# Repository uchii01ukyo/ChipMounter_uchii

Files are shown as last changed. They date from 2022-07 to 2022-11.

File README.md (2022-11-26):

# ChipMounter
電子部品を基板上の指定した位置に配置してくれる機構  
  
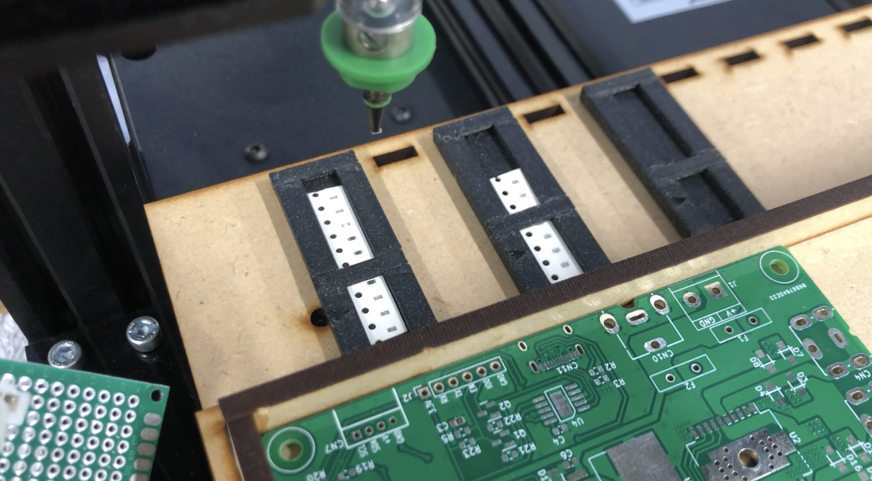
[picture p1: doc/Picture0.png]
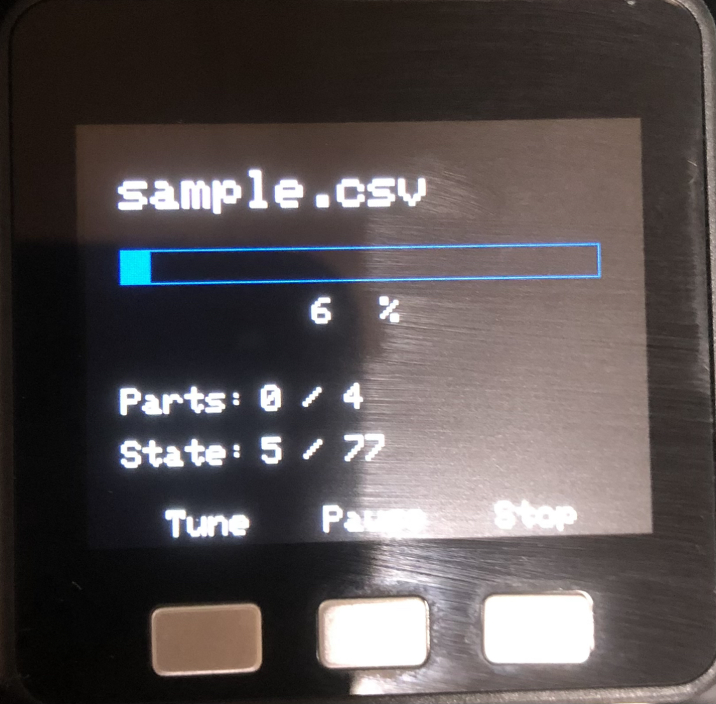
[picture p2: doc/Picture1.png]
  
  
3つのステップモーターでXYZ軸移動、別モーターでZ軸回転、吸引ポンプと吐出ポンプで部品のピッキングをしている．  
  
詳細：[ChipMounter_System.pdf](https://github.com/uchii01ukyo/ChipMounter_uchii/blob/master/doc/ChipMounter%20System.pdf)  
デモ：[demo0.mp4](https://github.com/uchii01ukyo/ChipMounter_uchii/blob/master/doc/demo0.mp4)    

以下のコードを参考にさせていただきました．  
参考：https://github.com/akita11/ChipMounter  

## 使い方
### CSVファイルの準備
実装部品の位置や角度はCSV形式のファイルから読みとる．  
1. KiCADから実装基板の部品情報（POSファイル）をCSVで出力する．  
2. CSVファイルの一番右に新しい行を挿入し、部品に対応するTrayIDを入力する．  
3. 「src/csv_gcode.py」の以下の部分をPOSファイルのパスに変更する．  
  
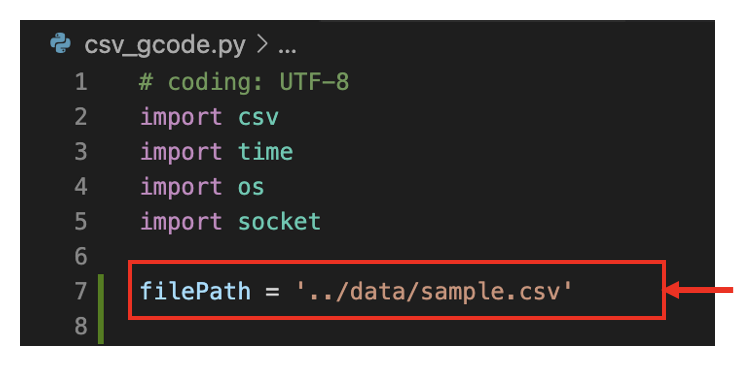
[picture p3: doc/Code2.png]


### 起動
1. M5Stackと使用するPCをUSBで接続する  
2. M5Stackを再起動する（画面に「Chip Mounter」が表示されている状態にする）  
3. start.commandを実行(クリックするだけでOK)  

### 起動後
起動後、PC上では２つのコマンドプロンプトが開かれ、GCODEの生成->送信が実行される．  
M5Stackではコマンドを受信し、それに合わせてアクチュエータ制御、画面表示等を実行する．  

## その他
### GRBLモジュールについて
非常にクセがあって苦労したので、ドキュメントを残すことにした．  
[M5Stack_GRBL_Module.pdf](https://github.com/uchii01ukyo/ChipMounter_uchii/blob/master/doc/M5Stack%20GRBL%20Module.pdf)  
  
### 注意
BOMおよびその他のデータは、著者によってのみテストされています。情報の不足や誤り、バグがある可能性があります。  
  
### テスト環境
以下の環境で実証済みです．
+ MacOS Big Sur (11.6.8)
+ Python 2.7.18
+ ArduinoIDE 1.8.13

## Author
Uchii Ukyo　(https://github.com/uchii01ukyo)

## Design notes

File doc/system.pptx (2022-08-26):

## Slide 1

PC

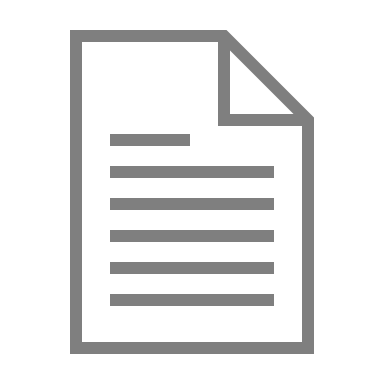
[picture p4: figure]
ドキュメント 枠線

M5Stack-CORE

M5_Serial.ino
GRBLControl.cpp
GRBLControl.h

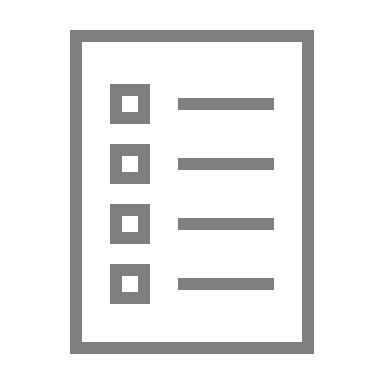
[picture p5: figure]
リスト 枠線

data.csv

read

UDP

Serial

csv_gcode.py

udp_serial.py

I2C
(0x70)

I2C
(0x71)

Digital
Write

GRBL-1

GRBL-2

Solenoid

Pump-1

X

Y

Z

R

Pump-2

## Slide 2

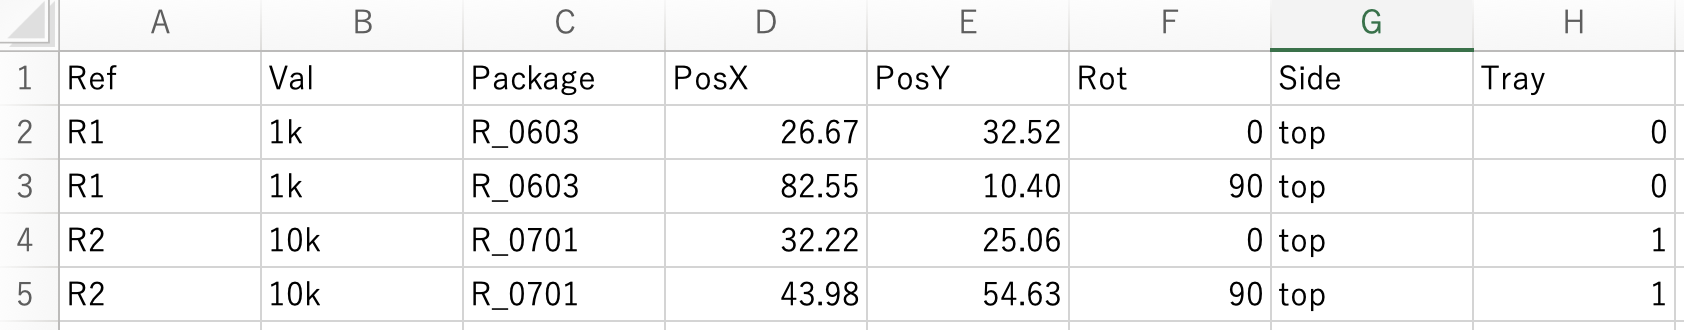
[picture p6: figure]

新しい行を挿入
→ TrayIDを入力

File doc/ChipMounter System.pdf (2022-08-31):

# ChipMounter System

全体のシステム概要図

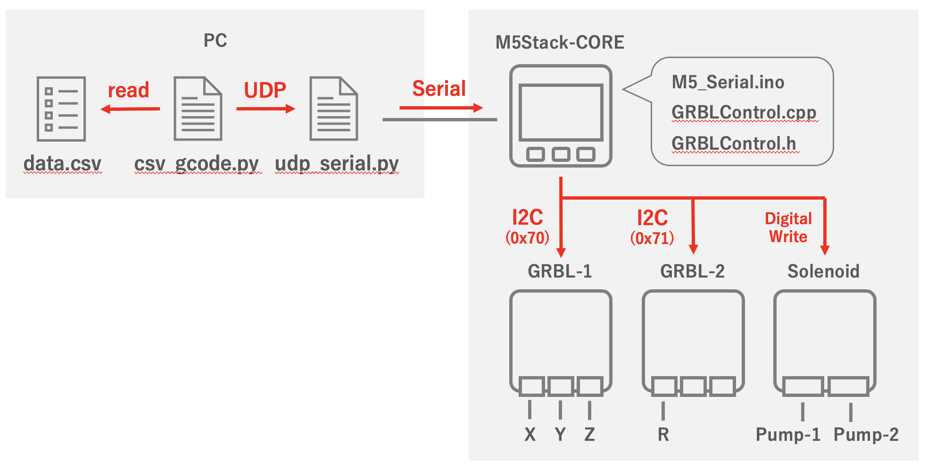
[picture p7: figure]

概要
- 制御するものは5つ
（X-StepMotor, Y-StepMotor, Z-StepMotor, 回転軸Motor, 吸ポンプ, 吐ポンプ）
- CSVで指定した部品位置に部品を配置する
- 作成したGcodeを、 udp_serial.py → M5_Serial.ino → GRBLの順に流すことでステップ モータ等を制御している

各コードの役割
- csv_gcode.py
= POSファイル（CSV形式）から、部品位置を抽出して、Gcodeを作成
= 作成したGcodeをUDP通信で送信
- udp_serial.py
= M5Stackとのシリアルを常時開通させ、Gcodeの送信、GRBLステータスの受信
- M5_Serial.ino
= Gcodeの受信、適切なモジュール（GRBL-1, GRBL-2, Soleoid）に送信
= 画面表示などのUI管理

## データ処理の流れ

## csv_gcodeの処理

処理の流れ
- CSVファイルから、POSデータ（部品の配置位置など）を読み取る
- POSデータからcommandを作成する
- 作成したcommandをudp_serial.py（UDP通信）、M5Stack-CORE（Serial通信）で受け渡 す
- 処理成功の合図（’ok’）を待ってから、次のcommandを送信
- commandを全部送信し切ったら、次の部品に関するPOSデータを取得しにいく

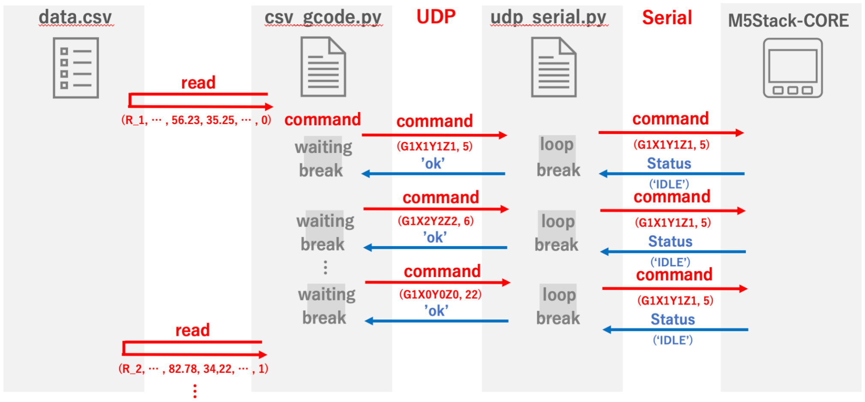
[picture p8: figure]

## udp_serial.pyの処理

処理の流れ
- csv_gcode.pyからcommandを受信する
- 受信したcommandをそのままM5Stack-COREに受け渡す
- スタータス確認コマンド（’@’）を送信して、現在のステータスを返してもらう
- ステータス’IDLE’を確認しだい、処理成功の合図として’ok’を送信する

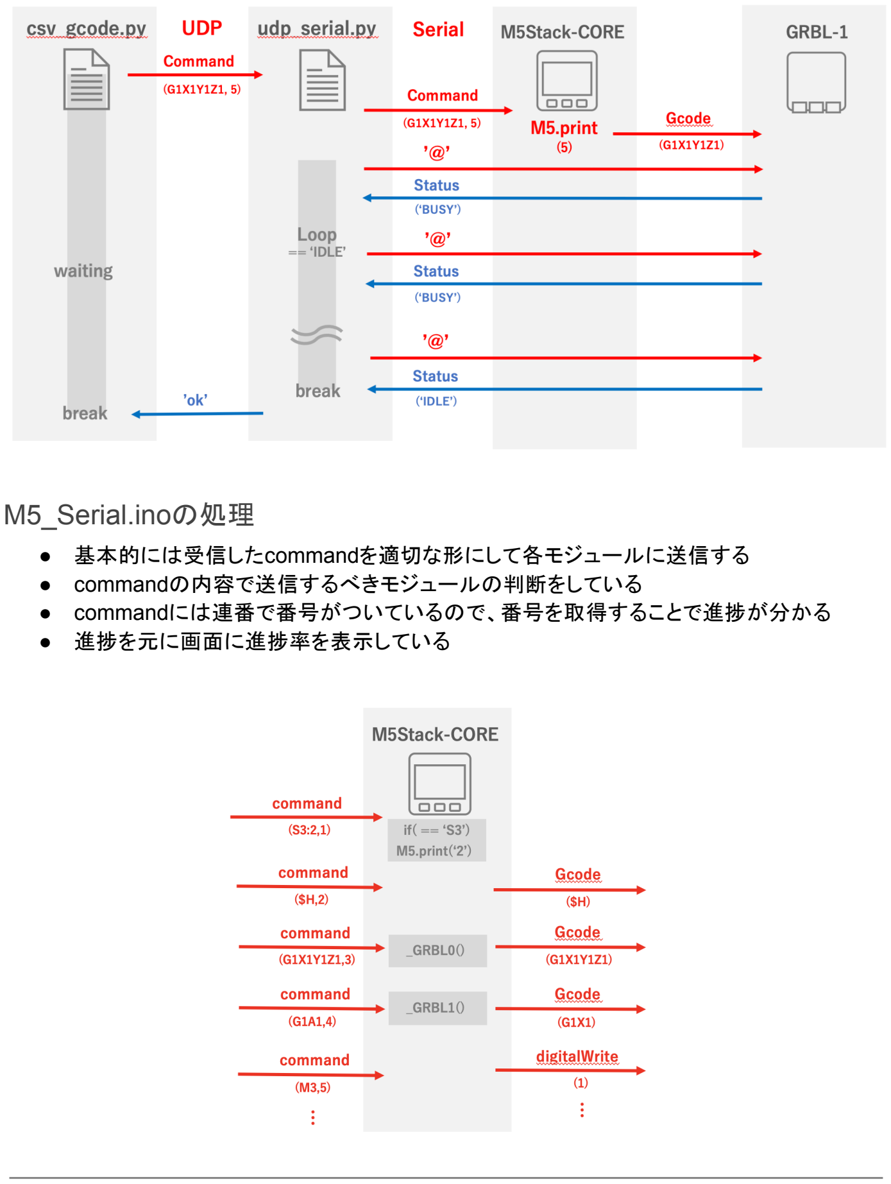
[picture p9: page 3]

## M5_Serial.inoの処理

- 基本的には受信したcommandを適切な形にして各モジュールに送信する
- commandの内容で送信するべきモジュールの判断をしている
- commandには連番で番号がついているので、番号を取得することで進捗が分かる
- 進捗を元に画面に進捗率を表示している

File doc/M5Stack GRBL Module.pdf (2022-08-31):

# M5Stack GRBL 13.2

2022.08.27 内井

公式ドキュメント：https://docs.m5stack.com/en/module/grbl13.2サンプルコード：https://github.com/m5stack/MODULE_GRBL13.2/tree/master

概要
- M5Stackで使用できるGRBLモジュール
- Motor Driver: DRV8825PWPR
- Controller Chip: ATmega328P-AU
- 1台で最大3つのステップモータを制御できる
- I2Cアドレスを変更すれば２台スタック可能
- 外部リミットスイッチを接続できる
- コマンドはGRBL0.8系で通用する

GRBL0.8系：https://github.com/grbl/grbl/wiki/Configuring-Grbl-v0.8

## はじめに

チップマウンター（基板部品を基板上に配置してくれる機構）を作ることに挑戦し、その時にGRBL を用いてステップモーターを制御するということをやった． そこでほぼ初めてGRBLを使ってモノづくりをしてみたが、以下の壁にぶつかった．

- GRBLについての情報がネットにあまり載っていない
（M5Stack GRBL 13.2に関する情報なんてほとんどない）
- いろんなバージョンが混ざってよく分からない
（Arduinoとか、CNCオープンソースとか．GRBLにも0.8系と0.9系と1.1系がある）
- そもそもGRBLについての基礎知識すらなくてよく分からない

とにかく情報がなく、公式ドキュメントを読めるだけの知識もなく、自力でしらみつぶしで検証する ことが多かった．
結局分からなかったものもあるが、多くは正解に辿り着いたと思う． 結果的に、公式ドキュメントが間違っていたり、公式のサンプルコードが間違っていたりと、いろい ろと穴だらけだった．またそもそも初心者つぶしのトラップがいくつも潜んでいることが分かった．

今後の自分のために、そして誰かのためにもドキュメントを残しておく．

## GCODE

初心者のために．そもそもGcodeとは何か、ステップモーターをどうやって動かすのか．

### ステップモータを動かす

動かし方１：
M5StackとArduinoIDEをUSBで接続する（シリアル通信ができる状態にする） M5StackにM5_serial.inoを書き込む
シリアルモニタの入力窓から、コマンドを入力する．
例えば、G91G0X1Y1Z1、と入力すれば現在位置から相対座標で（1,1,1）に動いてくれる．

動かし方２：
M5_Serial.inoのLoop関数内に、以下のコードを入れる． 「if(M5.BtnA.wasPressed()){ _GRBL0.Gcode(“G91G0X1Y1Z1”);」 M5StackとArduinoIDEをUSBで接続する（シリアル通信ができる状態にする） M5StackにM5_serial.inoを書き込む．
M5StackのAボタンを押す．

### ステップモータが動かない

いくつかよくあるミスを書いておく．

・供給されている電圧が低い / 電源が供給されていない パソコン給電ではなく、ACアダプタ等の外部電源が必要（適切な供給電圧で）

・配線がうまくされていない
ステップモーターには大きくユニポーラ式とバイポーラ式がある． またコードが途中で（親切心から）クロスしているものもある． ステップモータの種類によって配線が違うので、ドキュメントを見ながら配線する． 特に４線のうち真ん中２本がどう繋がっているかが問題になりやすい．違った場合は真ん中２本 だけをハンダで繋ぎかえるなどの対応をする

・GRBLライブラリが入っていない
ファームウェアはGRBLモジュール側に事前に書き込まれているため、不要． しかしM5Stack本体にはGRBLライブラリ（例えば、GrblControl.hとGrblControl.cppなど）を書き 込む必要がある．制御コードにインポートさせておくと良い．

・内部変数が適切でない
後述の内部変数の設定が適切でない場合がある．
（パルスが細かすぎてモータが動かない、トルクが足りなくて動かない等） 内部変数を見直してみると良い．

・ロックがかかっている
$17を1に設定していると、初めは必ずロック状態になる．ロック状態ではどの小アンドも機能し ない．$Xか$Hで解除してからコマンドを入力するか、初めから$17を0にしておく シリアル通信でコマンド”@”を送信すると、現在のステータスを返してくれる．「ALART」と返って きた場合は、ロック状態である可能性が高い．（問題なければ「IDLE」と返ってくる）

## 内部変数 / Internal variable

GRBLではモーターの速度やパルスの周期などのパラメータを事前に書きこんでおく． 各変数は書き込んだ時点で、自動でEEPROMに保存される． ただ何かのエラーの影響で、変数が知らない間に変更されることがあるので、挙動が急におかし くなった時は、変数が正常に設定されているか確認すると良い．

### 内部変数の設定方法

ArduinoIDEとGRBLモジュールをUSBでつなぐ（シリアル通信できるようにする） シリアルモニタを開いて、入力窓から直接入力するのが、一番簡単． 以下のようにArduino上に含めておけば、そこからモジュールに書き込むこともできる． （注意：一度に５つ以上の変数は設定できない）

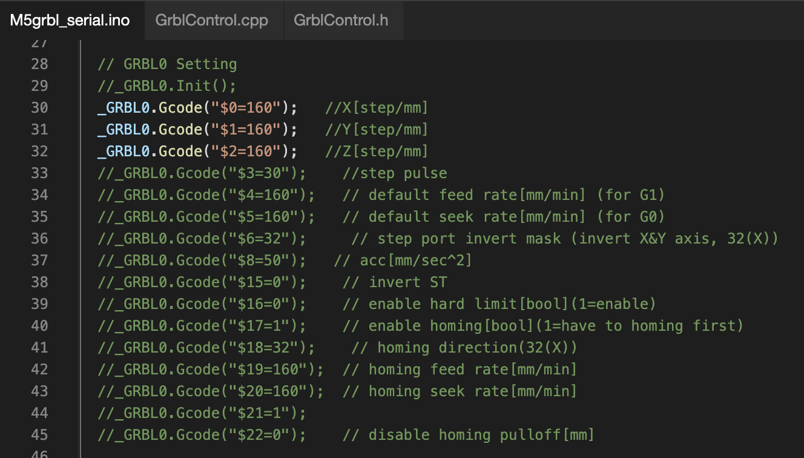
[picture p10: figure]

### 内部変数の設定

公式ドキュメントに記載されているものは誤りなので、気をつけること． Arduino式と設定内容が違うので注意すること（ネットのものはだいたいArduino式） 以下、実践の下、正しいと思われるものを載せる．

$0 = x [step/mm] 脱調（振動、騒音）している場合はここを変更すると良い
$1 = y [step/mm]
$2 = z [step/mm]
$3 = step pluse
$4 = feed rate [mm/min] (for G1)
$5 = seek rate [mm/min] (for G0)
$6 = step port invert mask 設定の仕方は後述 $8 = acc [mm/sec^2]
$10 = settings.mm_per_arc_segment
$11 = settings.n_arc_correction
$12 = settings.decimal_places

$13 = REPORT INCHES
$14 = BITFRAG_AUTO_START (=1)
$15 = invert ST (0=default, 1=モータの動作/停止が反対)
$16 = enable hard limit (0=disable, 1=enable)
$17 = enable homing (0=disable, 1=enable) 1だとhoming($H)されるまでlockされる $18 = settings.homing_dir_mask 設定の仕方は後述
$19 = settings.homing_feed_rate
$20 = settings.homing_seek_rate
$21 = settings.homing_debounce_delay homingを確かめる時間スパン[msec] $22 = settings.homing_pulloff homingした後に少し戻る

各変数について詳しい説明
（少し数字と内容が違うかもしれないが、参考程度に．） https://github.com/grbl/grbl/wiki/Configuring-Grbl-v0.8

## $6, $18の設定方法

$6 = default時の軸の正方向を指定する
$18= homing時の軸の正方向を指定する

各軸にビットが指定されている (X=5, Y=6, Z=7)． 1をこれだけビットシフトしたものの論理和として指定する．

分かりやすく言うと、
軸それぞれに以下の数字が与えられている
X = 00100000 (2進数表記) = 32 (10進数表記)
Y = 01000000 (2進数表記) = 64 (10進数表記)
Z = 10000000 (2進数表記) = 128 (10進数表記)

変更したい軸の数字を全て足したものを10進数で指定する． （例）
X軸だけを変更したい (32(X)なので) $6=32 X軸とY軸を変更したい (32(X)+64(Y)=96) $6=96 3軸ともに変更したい (32(X)+64(Y)+128(Z)) $6=224

### 内部変数を設定する時の注意点

モジュールのバッファサイズが小さいので注意

一般的なGRBLでは、コマンド “$$” を入力すると、内部変数の一覧を書き出してくれるようになっ ている（自分が過去に何を設定したかが分かるようになっている）．

M5Stack GRBL13.2でも同様のコマンドがあるが、バッファサイズの都合で10byteしか出力でき ない．なので、ほとんど見れない（$0〜$4くらいまでは見れる）．設定した数字はどこかにメモって おくか、しっかり設定できているか不安ならばその都度書き込むしかない．

また内部変数の設定は1つずつ行うのが最善．バッファサイズが10byteしかないので、一度に大 量の変数（5つ以上）を書き込むと全部書き込めない．オーバーした分は書きこまれないので注意 ．

## GRBLコマンド

GRBLは特定のコマンドを用いて操作する．
よく使うものをいくつか載せておく．
- $$ = 内部変数の書き出し
- $X = ロックの解除（$17=1でロックされている状態を解除する）
- $H = homing（原点復帰）を実行する
- F = feed rateを指定して移動（G0X1Y1Z1F200など）
- G0 = 単純移動（G0X1Y1Z1など）移動用で加工には向かない
- G1 = 直線移動（G1X1Y1Z1など）
- G90 = 絶対位置系で移動（G90G0X1Y1Z1など）
- G91 = 相対位置系で移動（G91G0X1Y1Z1など）
- G92X0Y0Z0 = 現在位置を原点に設定

他にも知りたい場合は以下の情報を参考にすると良い
（少し変数の内容が違うが、GRBL13.2モジュールにおいては、このドキュメントに書いてあるの が正しい）
- https://github.com/grbl/grbl/wiki/Configuring-Grbl-v0.8
- https://bbs.avalontech.jp/t/grbl-g/750/2

## リミットスイッチ

homingをするときなどにリミットスイッチを使う． （リミットスイッチにぶつかるまで動き続けるみたいな処理をする．）

一般的にリミットスイッチは、物理的な接触によって、内部スイッチが閉じる（または開く）ことに よって、信号を変化させ、ぶつかったことを知らせる．

モジュールに接続するには、リミットスイッチ3つ（X, Y, Z）を1つのコネクタにまとめなくてはいけな い．以下のように配線する．

COM = 3本それぞれのGNDと接続する
X = X軸スイッチの信号線（右側）
Y = Y軸スイッチの信号線（右側）
Z = Z軸スイッチの信号線（右側）

## DIPスイッチ

GRBLモジュールの中にDIPスイッチ（４つ並んでいるもの）が見える． そのスイッチを使って、マイクロステップ幅とI2Cアドレスを設定する．

マイクロステップは左側３つ（1,2,3番）の組み合わせで設定する 組み合わせは公式ドキュメントに載っている．

I2Cアドレスは一番右（4番）で設定する．
OFF側がDefaultアドレス（0x70）、ON側が代わりのアドレス（0x71）

## GRBL Tips

### GRBLの状態を知りたい

GRBLはGcodeを送信することで、ステップモータを制御することができる． しかし、Gcodeを送信するだけで終わりなので、処理が終了した合図は返ってこない． （前の処理が終わったら次のコマンドを送信するというデザインにしたいが、前の処理が終わった のかどうか誰も教えてくれない）

モーターの状態が今どうなっているのかを知ることはできない． （知るにはセンサーを入れてマイコンプログラムを書くことになる）

しかしGRBLモジュールがどうなっているのかは知ることができる． 基本的に、パソコン→M5Stackの向きでシリアル通信をして、Gcodeを送信している． GRBLの状態を知りたい時は、パソコン→M5Stackの方向にコマンド”@”を送信すれば、 M5Stack→パソコンの方向に現在のステータスを返してくれる．

ステータスはいくつかある．
・IDLE ＝ 待ち
・RUN ＝ 何かの処理を実行中
・BUSY = 何かの処理を実行中
・HOME = homing中
・ALARM = 警告またはロック状態をさす（ロック解除でIDLEに変わる）

参考

参考になった文献やサイトたち（閲覧：2022.08.27）

前述のものもあるが、最後にまとめてリンクを並べておいた．

M5Stack GRBL 13.2 公式ドキュメント https://docs.m5stack.com/en/module/grbl13.2

M5Stack GRBL 13.2 公式サンプルコード https://github.com/m5stack/MODULE_GRBL13.2/tree/master

GRBL0.8系について
https://github.com/grbl/grbl/wiki/Configuring-Grbl-v0.8

秋田純一先生のGitHubデータ
https://github.com/akita11/ChipMounter
- M5Stack GRBL 13.2 を使うためのライブラリ＆サンプルコード（動作確認済み） https://github.com/akita11/ChipMounter/tree/main/M5StackFW/M5grbl_serial
- M5Stack GRBL 13.2 に関する補足ドキュメント https://github.com/akita11/ChipMounter/blob/main/M5StackFW/M5GRBL_memo.md

秋田純一先生のチップマウンタ開発記録
https://note.com/akita11/n/ne17326245943

GCODEについて資料
https://bbs.avalontech.jp/t/grbl-g/750/2

ステッピングモーターの動作原理（動画）
https://www.youtube.com/watch?v=g18dOXJ1Lgc&t=4s

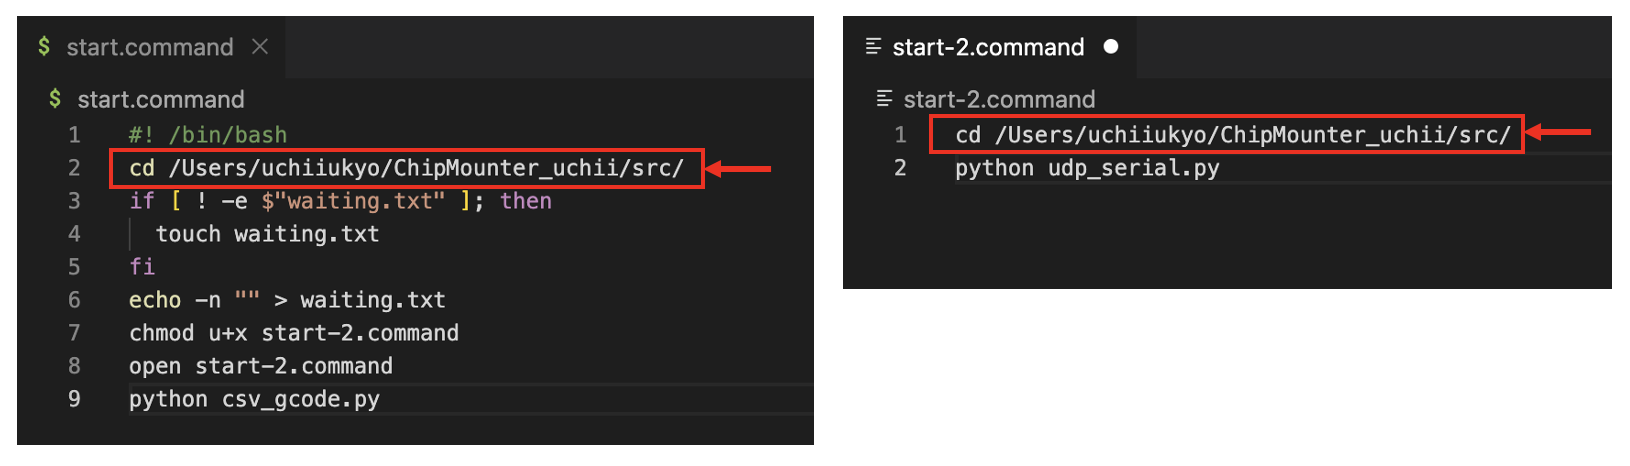
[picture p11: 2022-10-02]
doc/Code0.png

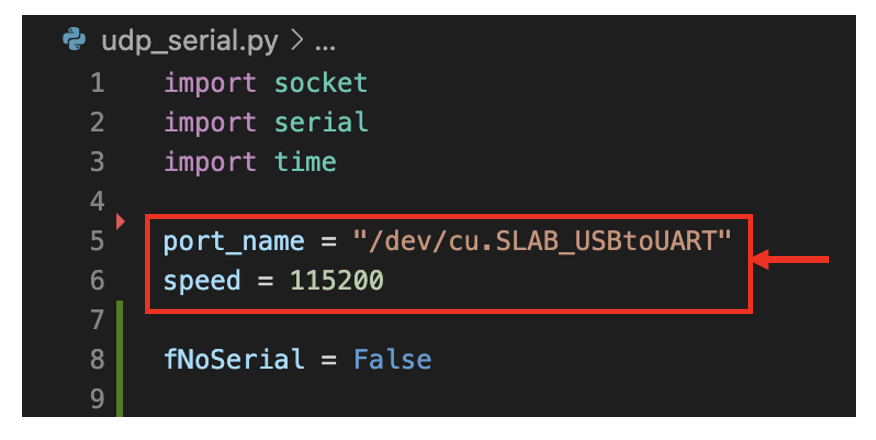
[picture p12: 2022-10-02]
doc/Code1.png

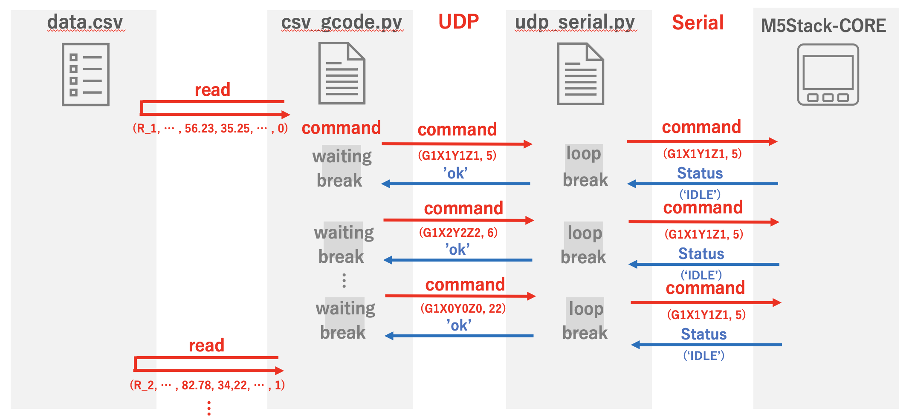
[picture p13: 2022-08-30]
doc/Picture2.png

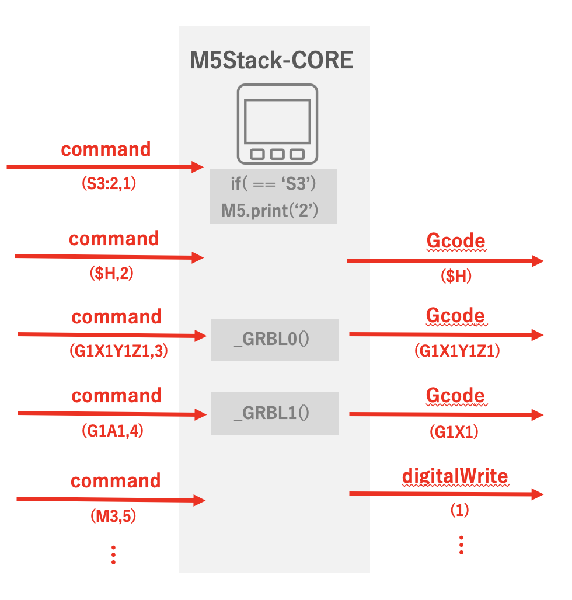
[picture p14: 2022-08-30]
doc/Picture5.png

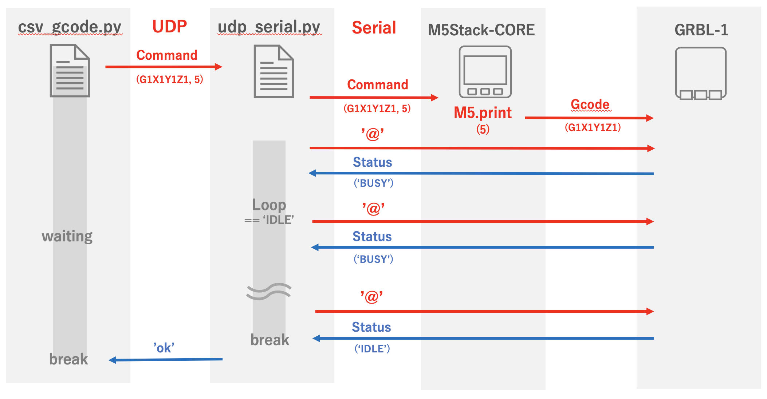
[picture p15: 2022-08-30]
doc/Picture3.png

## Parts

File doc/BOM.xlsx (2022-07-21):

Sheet: 購入リスト
チップマウンター開発
購入物リスト |  | 購入先 | 数量 | 単価 | 価格 | 購入日 | ステータス | 備考
3Dプリンタ | Tronxy XY-2 Pro | Amazon | 1 | 25999 | 25999 | 2021-10-05 | 到着 | https://www.amazon.co.jp/gp/product/B07YWJZMDD/
ソレノイドバルブ | 24V 1/4inch NPT | Amazon | 2 | 1529 | 3058 | 2021-10-05 | 到着 | https://www.amazon.co.jp/gp/product/B085NJFDWJ/
ダイアフラムポンプ |  | Amazon | 2 | 960 | 1920 | 2021-10-05 | 出荷待ち | https://www.amazon.co.jp/gp/product/B07F71S2B7/
ピックアップヘッド（セット） |  | Aliexpress | 1 | 10000 | 10000 | 2021-10-05 | 到着 | https://ja.aliexpress.com/item/32971863896.html?spm=a2g0s.9042311.0.0.39c84c4dtMK0tw
ニードルバルブ（6mmx2） |  | Amazon | 1 | 1112 | 1112 | 2021-10-05 | 到着 | https://www.amazon.co.jp/gp/product/B08LKTK1XN/
ホース（外径4mm） | 2m | Amazon | 1 |  |  | 2021-10-05 | 到着 | https://www.amazon.co.jp/gp/product/B019F8GQ32/
M5Stack GRBL |  | SwitchScience | 2 | 1925 | 3850 | 2021-10-05 | 到着
M5StackSolenoid |  | SwitchScience | 1 | 2200 | 2200 | 2021-10-05 | 到着 | ネジ端子に改造
USBカメラ |  | Aliexpress | 1 |  |  | 2021-10-05 | 到着 | https://www.amazon.co.jp/gp/product/B082Y55ZCG
NMEAケーブル(XH6-XH4) |  | Amazon | 3 | 1399 | 4197 | 2021-10-05 | 到着 | https://www.amazon.co.jp/gp/product/B07SHT5JD2/
ホース（外径6mm） |  | Amazon | 1 | 830 | 830 | 2021-10-29 | 発注 | https://www.amazon.co.jp/uxcell-%E3%83%8A%E3%82%A4%E3%83%AD%E3%83%B3%E3%83%81%E3%83%A5%E3%83%BC%E3%83%96-%E5%86%85%E5%BE%844mmx%E5%A4%96%E5%BE%846mm-%E5%85%A8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
購入予定
Tナット | M4 | Aliexpress |  |  |  |  |  | https://ja.aliexpress.com/item/4001305839607.html?spm=a2g0s.9042311.0.0.27424c4dLRbjA2
カメラ照明LED制御ボード |  | Akizuki | 1 | 150 | 150 |  |  | https://akizukidenshi.com/catalog/g/gK-13835/

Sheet: メモ
チップマウンター開発
買うもの | 発注 | 受取 | 品名 | メーカ・型番 | 購入先 | 個数 | 単価 | 参考（URL等）
○ | ○ | ○ | 3Dプリンタ | Tronxy XY-2 Pro | Amazon | 1 | 25999 | https://www.amazon.co.jp/gp/product/B07YWJZMDD/
○ | ○ | ○ | ソレノイドバルブ | 24V 1/4inch NPT | Amazon | 2 | 1529 | https://www.amazon.co.jp/gp/product/B085NJFDWJ/
ー |  |  | クイックコンタクト | NPT 1/4 6mm |  | 2 |  | https://ja.aliexpress.com/item/4000019598243.html?spm=a2g0s.9042311.0.0.27424c4dLRbjA2
ー |  |  | クイックコンタクト | NPT 1/4 4mm |  | 2 |  | https://ja.aliexpress.com/item/4000019598243.html?spm=a2g0s.9042311.0.0.27424c4dLRbjA2
○ | ○ |  | ダイアフラムポンプ |  | Amazon | 2 | 960 | https://www.amazon.co.jp/gp/product/B07F71S2B7/
○ | ○ |  | ピックアップヘッド（セット） |  | Aliexpress | 1 | 10000 | https://ja.aliexpress.com/item/32971863896.html?spm=a2g0s.9042311.0.0.39c84c4dtMK0tw
ー |  |  | Tジョイント（4mmx3） |  |  | 1
○ | ○ | ○ | ニードルバルブ（6mmx2） |  | Amazon | 1 | 1112 | https://www.amazon.co.jp/gp/product/B08LKTK1XN/
ー |  |  | ホース（内径8mm） | 1m |  | 1 |  | ホームセンターで買える
ー |  |  | ホース（外径6mm） | 1m |  | 1 |  | ホームセンターで買える
○ | ○ |  | ホース（外径4mm） | 2m | Amazon | 1 |  | https://www.amazon.co.jp/gp/product/B019F8GQ32/
ー |  |  | M5StackBasic |  |  | 1
○ | ○ |  | M5Stack GRBL |  | SwitchScience | 2 | 1925
○ | ○ | ○ | M5StackSolenoid |  | SwitchScience | 1 | 2200 | ネジ端子に改造
ー |  |  | DCプラグ2.1mm |  |  | 3 |  | M5StackSolenoidの電源を直結の場合は2個でもOK
ー |  |  | DC中継ジャック2.1mm |  |  | 1 |  | M5StackSolenoidの電源を直結の場合はなくてもOK
○ | ○Aliexpress |  | USBカメラ |  | Aliexpress | 1 | ? | https://www.amazon.co.jp/gp/product/B082Y55ZCG | https://ja.aliexpress.com/item/4000018914158.html?spm=a2g0s.9042311.0.0.7b264c4doocYnh
ー |  |  | USBハブ(2ポート) |  |  | 1
ー |  |  | USBケーブル | C-A |  | 1 |  | DAISOで買える
○ | ○ | ○ | NMEAケーブル(XH6-XH4) |  | Amazon | 3 | 1399 | https://www.amazon.co.jp/gp/product/B07SHT5JD2/ | ※ケーブル順序が違うので差し替えが必要
○ | ○ |  | カメラ照明LED制御ボード |  | Akizuki | 1 | 150 | https://akizukidenshi.com/catalog/g/gK-13835/
○ |  |  | 多回転抵抗 | 100Ω |  | 1 | ?
○ |  |  | カーボン抵抗 | 4Ω |  | 1 | ?
○ | ○ |  | チップLED | 白 | Akizuki | 12 | 400 | https://akizukidenshi.com/catalog/g/gI-03846/
ー |  |  | 偏光板 |  |  | 1 |  | 100均スマホ用偏光板でもOK
ー |  |  | チューブジョイント | 内径8mm-外径6mm |  | 2 |  | 3Dプリンタで成形してもOK
○ | ○ |  | Tナット | M4 | Aliexpress |  |  | https://ja.aliexpress.com/item/4001305839607.html?spm=a2g0s.9042311.0.0.27424c4dLRbjA2
ー |  |  | アクリル版 | 1.0mm |  |  |  | 100均スマホ用偏光板を使う場合は不要
ー |  |  | アクリル版 | 2.0mm
ー |  |  | アクリル版 | 3.0mm
ー |  |  | スパイラルチューブ |  |  |  |  | DAISOで買える
ー |  |  | ポンプ固定用バンド |  |  | 2 |  | 100均など。なくてもOK
ー |  |  | 色画用紙 | 緑 |  | 1 |  | DAISOで買える
ー |  |  | スプレー塗料 | つやけし黒 |  | 1
ー |  |  | マグネット |  |  | 4 |  | DAISOで買える(5個入り)
ー |  |  | ステンレス定規 | 30cm |  | 2 |  | DAISOで買える
ー |  |  | 厚紙 | 25x20cm |  | 1 |  | ステンレス定規と同じ厚さのもの
ー |  |  | シャーペン(0.2mm芯) |  |  | 1 |  | https://www.amazon.co.jp/gp/product/B019U2V96W/
ー |  |  | スペーサ | M3x10
ー |  |  |  | M3x5
ー |  |  |  | M3x8
ー |  |  | ネジ | M2
ー |  |  |  | M3
ー |  |  |  | M4
ー |  |  | M2ナイロンスタンドオフ | セット |  | 1 |  | https://www.amazon.co.jp/gp/product/B07V2M4H5M/

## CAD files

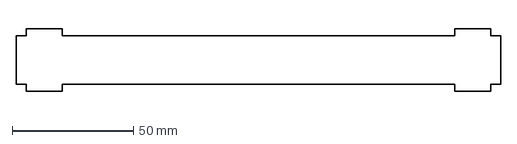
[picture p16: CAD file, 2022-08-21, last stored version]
parts/ChipMounter_3.dxf
200.0 x 26.0 mm

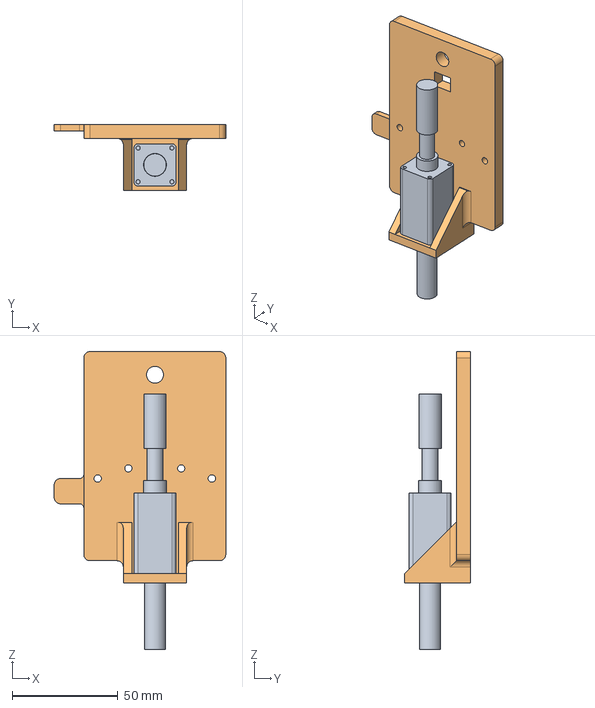
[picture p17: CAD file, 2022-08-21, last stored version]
parts/ChipMounter.step
81.2 x 31.0 x 141.0 mm
PickUpTool
JIG

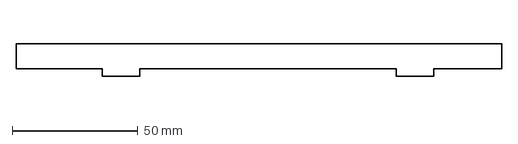
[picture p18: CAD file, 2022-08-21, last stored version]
parts/ChipMounter_2.dxf
192.8 x 13.0 mm

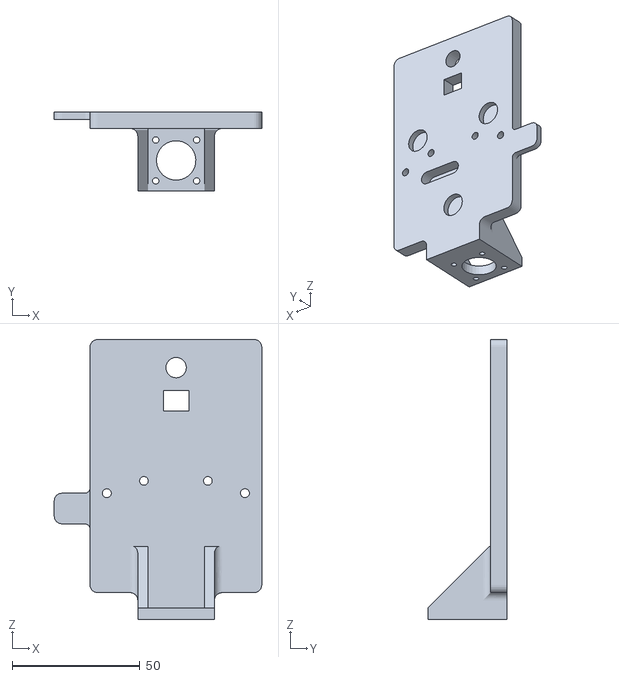
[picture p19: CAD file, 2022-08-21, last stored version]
parts/ChipMounter_jig.stl
81.2 x 31.0 x 109.5

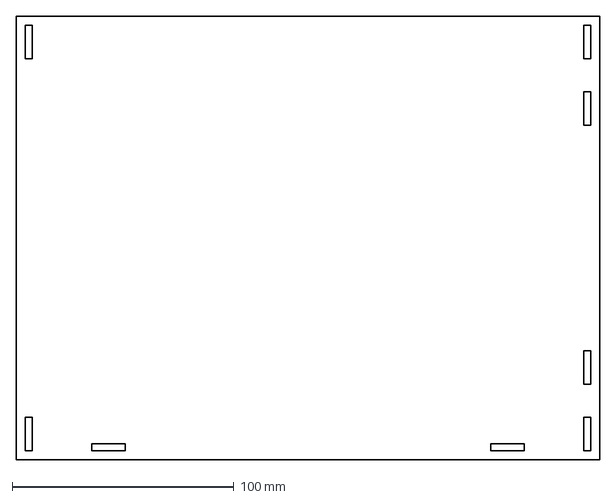
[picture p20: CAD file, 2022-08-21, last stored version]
parts/ChipMounter_4.dxf
263.0 x 200.0 mm

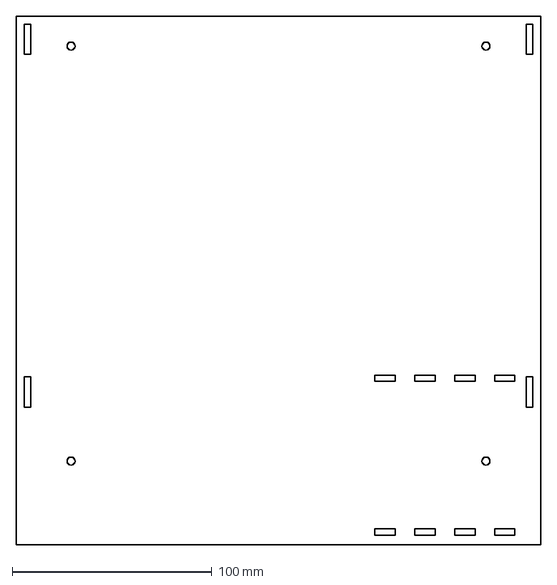
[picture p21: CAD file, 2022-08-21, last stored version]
parts/ChipMounter_5.dxf
263.0 x 265.0 mm

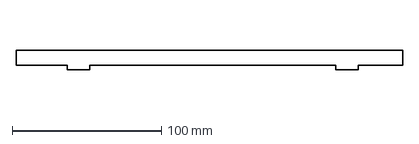
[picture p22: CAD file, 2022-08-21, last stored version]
parts/ChipMounter_1.dxf
258.9 x 13.0 mm

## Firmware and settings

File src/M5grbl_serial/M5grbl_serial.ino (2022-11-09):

#include <M5Stack.h>
#include "GrblControl.h"

#define I2C_ADDR0 0x70 // default address (1st)
#define I2C_ADDR1 0x71 // alternative address (2nd)

//#define SOL_A 26
#define SOL_B 12
//#define SOL_C 13
#define SOL_D 5

uint8_t fGRBL = 1, fwork=0, fpause=0, f_a=0;
int pos = 0, count;
char buf[1024], data[1024];
String fileName, totalParts, partsNum, code;
int totalCode=0;

GRBL _GRBL0 = GRBL(I2C_ADDR0);
GRBL _GRBL1 = GRBL(I2C_ADDR1);

void setup() {
  M5.begin();
  M5.Power.begin();
  Serial.begin(115200);
  initialError_LCD();
  while (Serial.available()) Serial.read(); // force serial buffer empty
  
  // GRBL0 Setting
  //_GRBL0.Init();
  //_GRBL0.Gcode("$0=160");   //X[step/mm]
  //_GRBL0.Gcode("$1=160");   //Y[step/mm]
  //_GRBL0.Gcode("$2=160");   //Z[step/mm]
  //_GRBL0.Gcode("$3=100");    //step pulse
  //_GRBL0.Gcode("$4=800");   // default feed rate[mm/min] (for G1)
  //_GRBL0.Gcode("$5=800");   // default seek rate[mm/min] (for G0)
  //_GRBL0.Gcode("$6=32");     // step port invert mask (invert X&Y axis, 32(X))
  //_GRBL0.Gcode("$8=50");   // acc[mm/sec^2]
  //_GRBL0.Gcode("$15=0");    // invert ST
  //_GRBL0.Gcode("$16=0");    // enable hard limit[bool](1=enable)
  //_GRBL0.Gcode("$17=1");    // enable homing[bool](1=have to homing first)
  //_GRBL0.Gcode("$18=32");    // homing direction(32(X))
  //_GRBL0.Gcode("$19=10");  // homing feed rate[mm/min]
  //_GRBL0.Gcode("$20=160");  // homing seek rate[mm/min]
  //_GRBL0.Gcode("$21=1");    // homing debounce[msec]
  //_GRBL0.Gcode("$22=0");    // disable homing pulloff[mm]

  // GRBL1 Setting
  //_GRBL1.Init();
  //_GRBL1.Gcode("$0=10");    //X[step/mm]
  //_GRBL1.Gcode("$3=30");    //step pulse
  //_GRBL1.Gcode("$4=600");   // default feed rate[mm/min] (for G1)
  //_GRBL1.Gcode("$5=1000");   // default seek rate[mm/min] (for G0)
  //_GRBL1.Gcode("$8=50");   // acc[mm/sec^2]
  //_GRBL1.Gcode("$17=0");    // enable homing[bool](1=have to homing first)
  //_GRBL1.Gcode("G91");      // relative mode for GRBL1
  
  // Solenoid Setting
  pinMode(SOL_B, OUTPUT); digitalWrite(SOL_B, 0);
  pinMode(SOL_D, OUTPUT); digitalWrite(SOL_D, 0);
  
  ReadGRBLstatus(0);
  ReadGRBLstatus(1);
  initial_LCD();
}

void ReadGRBLstatus(int ch) {
  String s;
  if (ch == 0) s = _GRBL0.ReadLine();
  //if (ch == 1) s = _GRBL1.ReadLine();
  Serial.print(s);
}

void loop() {
  char c;
  int ch, i;
  
  M5.update();
  
  if (M5.BtnA.wasPressed()) {
    if(fwork==1){
      if(f_a==0){
        f_a=1;
        M5.Lcd.setTextColor(RED, BLACK);
      }else{
        f_a=0;
        M5.Lcd.setTextColor(WHITE, BLACK);
      }
      M5.Lcd.setCursor(45, 220);
      M5.Lcd.println("Tune");
    }
  }
  
  if (M5.BtnB.wasPressed()) {
    if(fwork==1){
      if(fpause==0){
        fpause=1;
        M5.Lcd.setTextColor(RED, BLACK);
      }else{
        fpause=0;
        M5.Lcd.setTextColor(WHITE, BLACK);
      }
      M5.Lcd.setCursor(135, 220);
      M5.Lcd.println("Pause");
    }
  }
  
  if (M5.BtnC.wasPressed()) {
    if(fwork==1){
      if(fpause==0){
        fpause=1;
        M5.Lcd.setTextColor(RED, BLACK);
        _GRBL0.Gcode("G90G1Z0F800");
        _GRBL0.Gcode("G90G1X0Y0F800");
        _GRBL0.Gcode("finish");
        stop_LCD();
        fwork=0;
      }
    }
  }
  
  while (Serial.available()) {
    c = Serial.read();
    if (c == '\r' || c == '\n') {
      fGRBL = 1;
      buf[pos] = '\0';
      if (pos > 0 && (buf[pos - 1] == '\r' || buf[pos - 1] == '\n')) buf[pos - 1] = '\0';
      if (pos != 0) {Serial.print('['); Serial.print(buf); Serial.println(']');}

      split(buf, ',', pos); // buf(char[1024]) -> data(char[1024]), code(String)
      if(code!="" && fwork==1) progress(code);

      /*if(data[0]=='@'){
        check_pause();
        fGRBL = 0;
      }*/
      if (data[0] == 'S') {
        S_command(data);
        fGRBL = 0;
      }
      if (data[0] == 'M') {
        fGRBL = 1;
        if (data[1] == '3') digitalWrite(SOL_B, 1);      // M3:Solnenoid B on
        else if (data[1] == '5') digitalWrite(SOL_B, 0); // M5:Solnenoid B off
        else if (data[1] == '7') digitalWrite(SOL_D, 1); // M7:Solnenoid D on
        else if (data[1] == '9') digitalWrite(SOL_D, 0); // M9:Solnenoid D off
      }
      if (fGRBL == 1 && fpause == 0) {
        ch = 0;
        // A/B/C axis -> GRBL1's X/Y/Z axis
        for (i = 0; i < pos; i++) {
          if (data[i] == 'A') {ch = 1; data[i] = 'X';}
          if (data[i] == 'B') {ch = 1; data[i] = 'Y';}
          if (data[i] == 'C') {ch = 1; data[i] = 'Z';}
        }
        Serial.print(ch); Serial.print(' '); Serial.println(data);        
        if (ch == 0) {
          _GRBL0.Gcode(data);
          ReadGRBLstatus(0);
        }
        else {
          _GRBL1.Gcode(data);
          ReadGRBLstatus(1);
        }
      }
      data[0]='\0';
      pos = 0;
    }
    else buf[pos++] = c;
  }
}


void progress(String code){
  int code_int=code.toInt();
  if(totalCode!=0){
    float percent=100*(code_int)/(totalCode);
    if(percent<0) percent=0;
    if(percent>100) percent=100;
    M5.Lcd.progressBar(20,70,280,20,percent); // posX, posY, width, height 
    m5.Lcd.setTextSize(2);
    M5.Lcd.setCursor(100, 180);
    M5.Lcd.println(String(code_int) + " / " + String(totalCode));
    M5.Lcd.setCursor(130, 100);
    M5.Lcd.println(int(percent));
    M5.Lcd.setCursor(170, 100);
    M5.Lcd.println("%");
  }
}

void initialError_LCD(){
  M5.Lcd.clear();
  M5.Lcd.setTextColor(WHITE, BLACK);
  M5.Lcd.setBrightness(100);
  M5.Lcd.setTextSize(3);
  M5.Lcd.setCursor(110, 80);
  M5.Lcd.println("Error");
  M5.Lcd.setTextSize(2);
  M5.Lcd.setCursor(15, 160);
  M5.Lcd.println("GRBL-Modules are not set");
}

void initial_LCD(){
  M5.Lcd.clear();
  M5.Lcd.setTextColor(WHITE, BLACK);
  M5.Lcd.setBrightness(100);
  M5.Lcd.setTextSize(3);
  M5.Lcd.setCursor(50, 80);
  M5.Lcd.println("Chip Mounter");
  M5.Lcd.setCursor(150, 120);
  M5.Lcd.println("+");
  M5.Lcd.setTextSize(2);
  M5.Lcd.setCursor(35, 160);
  M5.Lcd.println("Run the command file");
}

void work_LCD(){
  M5.Lcd.clear();
  M5.Lcd.setTextSize(2);
  M5.Lcd.setCursor(45, 220);
  M5.Lcd.println("Tune");
  M5.Lcd.setCursor(135, 220);
  M5.Lcd.println("Pause");
  M5.Lcd.setCursor(235, 220);
  M5.Lcd.println("Stop");
  M5.Lcd.setCursor(20, 150);
  M5.Lcd.println("Parts:");
  M5.Lcd.setCursor(20, 180);
  M5.Lcd.println("State: ");
}

void stop_LCD(){
  M5.Lcd.clear();
  M5.Lcd.setTextColor(WHITE, BLACK);
  M5.Lcd.setBrightness(100);
  M5.Lcd.setTextSize(3);
  M5.Lcd.setCursor(60, 80);
  M5.Lcd.println("Stop Command");
  M5.Lcd.setTextSize(2);
  M5.Lcd.setCursor(60, 140);
  M5.Lcd.println("Operation stopped!");
  M5.Lcd.setCursor(15, 180);
  M5.Lcd.println("Please restart to resume");
}

void S_command(char data[1024]){
  fwork=1;
  if(data[1]=='1'){
    work_LCD();
    fileName = data;
    fileName.replace("S1:", "");
    M5.Lcd.setTextSize(3);
    //if(sizeof(fileName)>16){fileName[16]== '\0'; M5.Lcd.println("IN");}
    M5.Lcd.setCursor(20, 25);
    M5.Lcd.println(fileName);
  }
  if(data[1]=='2'){
    totalParts = data;
    totalParts.replace("S2:", "");
    totalCode=totalParts.toInt()*17+7;
  }
  if(data[1]=='3'){
    partsNum = data;
    partsNum.replace("S3:", "");
    m5.Lcd.setTextSize(2);
    M5.Lcd.setCursor(100, 150);
    M5.Lcd.println(String(partsNum) + " / " + totalParts);
  }
}


void split(char buf[1024], char delimiter, int number){
  int mode = 0;
  int index=0;
  int i=0;
  code="";
  for(i = 0; i < number; i++){
    char tmp = buf[i];
    if(tmp == delimiter){
      mode=1;
      index=i+1;
    }else{
      if(mode==0) data[i]=tmp;
      if(mode==1) code = code + tmp;
    }
    data[i+1] = '\0';
  }
}

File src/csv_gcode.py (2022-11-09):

# coding: UTF-8
import csv
import time
import os
import socket

filePath = '../data/sample.csv'

# ---- Fabrication Setting [mm] ----
home=[0.000 , -6.600, -2.000] # X,Y,Z
trayPosX=[30.596, 51.012, 70.152, 90.249, 110.346, 130.443, 149.902]
trayPosY=-27.748
tray_down=-9.000
board_down=-4.600
shiftX=3.800; shiftY=2.000; feed=4.000 # tray
#
pulse=[31.900, 31.400, 6.440, 1.000] # [mm/G1X1], [mm/G1Y1], [mm/G1Z1], [mm/G1A1]=18
# --------- UDP Setting ----------
# global udpSock, Client_Addr, UDP_SERIAL_Addr
Client_IP = "127.0.0.1"
Client_Port = 10031
Client_Addr = (Client_IP, Client_Port)
UDP_SERIAL_IP = "127.0.0.1"
UDP_SERIAL_Port = 10030
UDP_SERIAL_Addr = (UDP_SERIAL_IP, UDP_SERIAL_Port)
UDP_BUFSIZE = 1024
# 
udpSock = socket.socket(socket.AF_INET, socket.SOCK_DGRAM)
udpSock.bind(Client_Addr)
udpSock.settimeout(1)
# --------------------------------
code_count=0

def main():
    # UDP waiting
    waiting_udp()

    send_serial('S1:' + str(get_fileName(filePath)))
    send_serial('S2:' + str(get_totalLine(filePath)))
    send_serial('S3:0')

    # GCODE
    start_gcode()
    count=0
    with open(filePath, 'r') as f:
        reader = csv.reader(f)
        header = next(reader)  # skip header
        for line in reader:
            count+=1
            print("Parts count: " + str(count))
            print(line)
            generation_gcode(line[3], line[4], line[5], line[7])
            send_serial('S3:' + str(count))
    finish_gcode()


def mm_gcode(mm,axis):
    if(axis=='X'):
        gcode = float(mm)/pulse[0]
    elif(axis=='Y'):
        gcode = float(mm)/pulse[1]
    elif(axis=='Z'):
        gcode = float(mm)/pulse[2]
    elif(axis=='R'):
        gcode = float(mm)/pulse[3]
    gcode_str=str(round(gcode, 3))
    return gcode_str

def generation_gcode(posX, posY, rot, trayNum):
    # send_serial("G90G1X0Y0F800")  # up
    send_serial("G90G1X" + mm_gcode(trayPosX[int(trayNum)]-shiftX,'X') + "Y" + mm_gcode(trayPosY+shiftY,'Y') + "F100") # trayhole
    send_serial("G90G1Z" + str(tray_down) + "F200") # down
    send_serial("G90G1Y" + mm_gcode(trayPosY+shiftY+feed,'Y') + "F50") # feeder
    send_serial("G90G1Z" + str(tray_down+2) + "F200")  # up
    send_serial("G90G1X" + mm_gcode(trayPosX[int(trayNum)],'X') + "Y" + mm_gcode(trayPosY,'Y') + "F50") # tray
    send_serial("G90G1Z" + str(tray_down) + "F200") # down
    send_serial("M3")  # pump ON
    send_serial("G90G1Z0F200")  # up
    send_serial("G90G1X" + mm_gcode(posX,'X') + "Y" + mm_gcode(posY,'Y') + "F100") # set position
    send_serial("G91G1A" + mm_gcode(rot,'R'))   # rotation
    send_serial("G90G1Z" + str(board_down) + "F200") # down
    send_serial("M5")               # pump OFF
    send_serial("M7")               # pump ON
    time.sleep(0.05) # waiting
    send_serial("M9")               # pump OFF
    send_serial("G90G1Z0F200")  # up

def start_gcode():
    send_serial("$X") # unlock
    send_serial("$H") # homing
    send_serial("G92X0Y0Z0") # origin setting
    send_serial("G90G1X" + str(home[0]) + "Y" + str(home[1]) + "F100") # origin
    send_serial("G90G1Z" + str(home[2]) + "F200") # origin
    send_serial("G92X0Y0Z0") # origin setting

def finish_gcode():
    send_serial("G90G1Z0F200")  # up
    send_serial("G90G1X0Y0F100") # home
    send_serial("finish") # finish

def get_totalLine(filePath):
    with open(filePath) as myfile:
        totalLines = sum(1 for line in myfile) - 1
    return totalLines

def get_fileName(filePath):
    fileName = os.path.basename(filePath)
    return fileName

def send_serial(cmd):
    # global udpSock, UDP_SERIAL_Addr
    global code_count
    code_count=code_count+1
    command = cmd + ',' + str(code_count)
    print(command)
    udpSock.sendto(command.encode('utf-8'), UDP_SERIAL_Addr)

    while True:
        try:
            data, addr = udpSock.recvfrom(UDP_BUFSIZE)
        except:
            pass
        else:
            if data.decode() == "ok":
                print("-> OK")
                break

def waiting_udp():
    print("wait")
    while True: 
        f = open('waiting.txt', 'r')
        data = f.read()
        f.close()
        if(data=='OK'):
            break
        print("wait")
        time.sleep(0.5) # waiting
    print("OK")

if __name__ == '__main__':
    main()
